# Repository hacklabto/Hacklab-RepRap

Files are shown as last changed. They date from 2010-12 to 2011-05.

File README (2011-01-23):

Prusa Mendel

Please read http://reprap.org/wiki/Hacklab_RepRap before attempting to build this.

When checking out from git, run the following to check out the MCAD dependencies:
	git submodule init
	git submodule update

Frame vertexes are based on Viks and Tonokips ones

Prusa Mendel part list:

To print:

6x frame-vertex
2x coupling
3x endstop-holder
1x x-carriage
1x x-end-idler
1x x-end-motor
2x z-motor-mount
4x belt-clamp
8x bar-clamp
2x rod-clamp
1x y-motor-bracket
2x pulley

3x pla-bushing

The Mendel build plate contains all the parts except the pla bushings

Vitamins required:

5/16 threaded rods - Measure these by assembling your parts to the build size you need and then figure out how long the rods need to be. (this sucks i know.. it's beta ;)
5/16 smooth rods - same
5/16 nuts - allot? I'd say 50-75?
some zip ties
teflon bushings
screws for your motors
4x nema 17 stepper motors
2x XXmm x 5mm T5 pitch timing belt

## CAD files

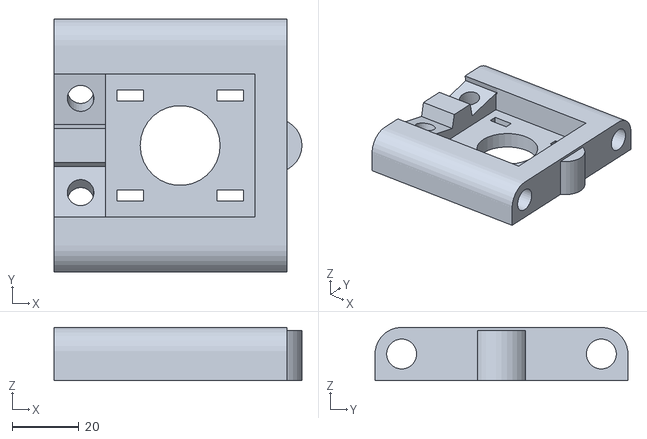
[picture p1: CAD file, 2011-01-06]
bin/z-motor-mount.stl
74.5 x 76.0 x 16.0

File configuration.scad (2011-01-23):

// PRUSA Mendel  
// Configuration file
// GNU GPL v2
// Josef Průša
// josefprusa@me.com
// prusadjs.cz
// http://www.reprap.org/wiki/Prusa_Mendel
// http://github.com/prusajr/PrusaMendel

//include <lib/mcad/motors.scad>
include <lib/mcad/nuts_and_bolts.scad>
include <constants.scad>

$fs= 0.3;

// Frame Design Settings
//=================

x_belt = true; //use belt or threaded rod for x-axis movement
               //threaded rod is currently broken. Do not use it.
               //Leave this true or be prepared to do lots of drilling!
               //Also, x-carriage doesn't support this option so you'll
               //have come up with a hack to make it work if you use this
               //option.

two_top_rods = true; //Use two top rods or one?
                      //No repraps have been built with one top, so use
                      //this design at your own risk!


//Spacing of the 2 smooth rods that the x carriage rides on
x_rod_spacing = 50;


// Build Volume Settings
//=================

//The x,y and z printable dimensions in that order
build_volume = [100,100,70];



// Threaded Rod Settings
//=================

//the diameter of the threaded rods
threaded_rod_diameter = 9;

//the radius of plastic needed around each threaded rod hole
//to hold it in place
threaded_rod_horizontal_clearance = 4;

//the plastic needed above and under each threaded rod hole
threaded_rod_vertical_clearance = 2;

nut_diameter=METRIC_NUT_AC_WIDTHS[8];//13.5;
nut_thickness = METRIC_NUT_THICKNESS[8]; //7.8;


tear_shape = false; //Use tear shaped holes for rods? not compatable with tight_grip = true

tight_grip = false; // Use tight holes where possible so that parts will self tap when 
                   // threaded rod is drilled in. Reduces need for nuts.
                   // tight_grip = false not compatable with two_top_rods = false



// Motor Settings
//=================

//NEMA_version //Variable not yet implemented.



//BS That Works
//=================

// unprintable height under the y carriage for motors + electronics.
// (rough estimate for vert angle calculations)
basement_height = 90;

// unprintable height from the bottom of the top frame vertex to 
// the point where the frame verticies meet.
// (rough estimate for vert angle calculations)
attic_height = 5;

//unprintable area due to the x ends/z-sliders
z_slider_unprintable_height = 70;

// extra length needed on the y axis to compensate for the 
// y-carriage's length. This is setup for the ABP carriage mount.
y_carriage_unprintable_length = 4;

//length from the middle of the bottom frame vertex to where the 
//frame triangle's threaded rods would meet if they were 
//extended to that point.
y_vert_triangle_offset = 2;

total_unprintable_area = [0,
	y_carriage_unprintable_length + y_vert_triangle_offset,
	basement_height+attic_height+z_slider_unprintable_height];


// Driven Dimensions [NO USER-CONFIGURABLE OPTIONS]
//=================

vert_angle = atan( 2*(build_volume[Z]+total_unprintable_area[Z])/(build_volume[Y]+total_unprintable_area[Y]));

echo("Frame Vertex Angle: ",vert_angle);

hor_hole_seperation = threaded_rod_diameter*2+threaded_rod_horizontal_clearance*2;



// Legacy
//=================

// DEPRECATED! M8 rod diameter. use threaded_rod_diameter
m8_diameter = threaded_rod_diameter;

// Used for $fn nut trick -> cylinder(h = 5, r=4.5, $fn=6, center=true);

//Diameter of the nuts used on the the threaded rod
//nut_diameter = 16.4;
//Clearance for accessible nuts such as on frame verticies
nut_clearance = 4;

//DEPRECATED! use nut_diameter
// M8 nut diameter diameter.
m8_nut_diameter = nut_diameter;

// M4 rod/screw diameter
m4_diameter = 5;

// M4 nut diameter diameter
// Used for $fn nut trick -> cylinder(h = 5, r=4.5, $fn=6, center=true);
m4_nut_diameter = METRIC_NUT_AC_WIDTHS[4]; //9;

// M3 rod/screw diameter
m3_diameter = 4.4;

// M3 nut diameter diameter
// Used for $fn nut trick -> cylinder(h = 5, r=4.5, $fn=6, center=true);
m3_nut_diameter = METRIC_NUT_AC_WIDTHS[3]; //7;

// Bushing holders diameter
bushing_diameter = 11;

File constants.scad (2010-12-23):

X = 0;
Y = 1;
Z = 2;

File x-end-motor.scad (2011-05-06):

// PRUSA Mendel  
// X-end with idler mount
// GNU GPL v2
// Rob Gilson, Christopher Olah
// http://reprap.org/wiki/Hacklab_RepRap
// https://github.com/hacklabto/Hacklab-RepRap

include <configuration.scad>
include <common.scad>
include <lib/mcad/nuts_and_bolts.scad>

thickness = 15;
length = 50;
width = 47.5;

bearing_inner_diameter = 7.5;

difference()
{
	union()
	{
		cube([width, length, thickness], center=true);
		//idler mount
		translate([width/2-2.5,width-4,-1])
			cube([5,47,45],center=true);
	}

	//holes for axis
	translate([0,-39,0]) x_axis_rods();
	for (x=[-1,1]) for(y=[-1,1]) translate([x*15,y*15,0]) ziptie_hole(thickness+1);
	translate([0,0,2]) z_nut_and_bushing_hole(thickness+1);
	#translate([width/2-11,width-1,-1]) rotate([0,-90,0]) motor();

}

module ziptie_hole(height)
{
	cube([5,10,height], center=true);
}

nut_and_bushing_seperation = 20;

module z_nut_and_bushing_hole(height=100)
{
	nut_radius = METRIC_NUT_AC_WIDTHS[8]/2+0.1;

	translate([0,-1.5*nut_radius-2]){
		cylinder(r=10, h=height, center=true);
		cylinder(r=4.3, h=1.5*height, center=true);
	}
	for (i=[1.4,1.5,1.6,1.75,1.9,2.0,2.1]) translate([0,i*nut_radius]){
		cylinder(r=4.3, h=1.5*height, center=true);
		linear_extrude(height = height, center = true)
			rotate(90) nutHole(size = 8, tolerance = +0.1, proj=1);
	}
	
}

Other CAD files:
y-end-motor-leadscrew.scad
bearing-pulley.scad
common.scad
coupling.scad
makerbot.scad
partlist.scad
prusalogo.scad
sanity_check.scad
vertex.scad
vertical-bar-clamp.scad
x-carriage-mendel.scad
x-carriage-mini.scad
x-carriage.scad
x-end-idler.scad
y-carriage-abp.scad
y-carriage-bushings.scad
y-carriage.scad
y-end-motor.scad
z-motor-mount.scad

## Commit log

2010-10-19 Initial add of Makefile and conditional rendering to makerbot.scad.
    [makerbot.scad]
2010-10-19 Reworked Makefile. Removed STL files created by scad or pulled from other sources (e.g. nophead pulley.stl).
    [bar-clamp.stl, belt-clamp.stl, coupling.stl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]
2010-11-13 UNTESTED: Lattice bottoms to avoid warping on x-carriage, x-end-motor. (Idea from clothbot.)
    [x-carriage.scad, x-end-motor.scad]
2010-11-13 Fixed stls, changed dicetion of x-carriage lattice.
    [x-carriage.scad, x-carriage.stl]
2010-11-13 Added x-end-motor.stl
    [x-end-motor.stl]
2010-11-13 Lattice replaced with a couple large grooves that should prevent warping similarily and be much easier to print in x-end-motor.
    [x-end-motor.scad, x-end-motor.stl]
2010-11-13 Grooves on x-carriage. Still not tested.
    [x-carriage.scad, x-carriage.stl]
2010-11-14 Revert "Lattice replaced with a couple large grooves that should prevent warping similarily and be much easier to print in x-end-motor."
    This reverts commit a599a914dad5de719b904652a9f80c7adc6e9a6b.
    [x-end-motor.scad, x-end-motor.stl]
2010-11-14 Some stuff from topmerge2 got into master. Can't seem to get rid of it. Commiting to change branches.
    [z-motor-mount.scad]
2010-11-16 Reworked top joint, reduces printed part count by 4, reduces knuts by self tapping threaded parts, and gets rid of one rod.
    [z-motor-mount.scad, z-motor-mount.stl]
2010-11-16 And this adds the one rod top version.
    [z-motor-mount-onerod.scad, z-motor-mount-onerod.stl]
2010-11-16 Minor cleanup, fixes.
    [z-motor-mount-onerod.scad, z-motor-mount-onerod.stl, z-motor-mount.scad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]
2010-11-16 Added z-motor-mount-onerod to Makefile.
2010-11-16 Merged z-motor-mount-onerod and z-motor-mount.
    [z-motor-mount-onerod.scad, z-motor-mount.scad]
2010-11-20 Added mcad with appropriate path changes.
    [configuration.scad]
2010-11-20 x-end-motor supports rod in place of belt, config and motor design for x-end-motor, z-motor-mount, motor design moved to configuration.scad.
    [configuration.scad, x-end-motor.scad, z-motor-mount.scad]
2010-11-20 Add x-bar support to x-end-motor.
    [x-end-idler.scad]
2010-11-21 the threaded x movement bar is broken. So I've made it *not* the default option. You can use it if you'd like, but you'll have to do lots of drilling.
    [configuration.scad]
2010-11-21 Y leadscrew motor mount, untested
    [configuration.scad, y-end-motor.scad]
2010-11-25 New 2 peice motor/leadscrew shaft coupler with zip ties and better shaft alignment
    [configuration.scad, coupling.scad]
2010-11-27 Began abstracting commmon components into common.scad, in particular, bar interfaces have been to ensure all parts will comply with standards.
    x_belt=false is still broken, though x-end-motor is done.
    [common.scad, configuration.scad, x-end-idler.scad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]
2010-11-28 x-end-idler is fixed. Yay!
    [configuration.scad, x-carriage.scad, x-end-idler.scad]
2010-11-30 Slimmed down x-end-idler.
    [x-end-idler.scad]
2010-12-18 y-carriage added for ABPs and frame vertex redesign for angle configuration and less wasted vertical space
    [configuration.scad, frame-vertex.scad, vertex-body-fixed-qcad.dxf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]
2010-12-18 x-end-idler redesign. Temporarily broken until x-end-motor catches up.
    [configuration.scad, x-end-idler.scad]
2010-12-18 Added a sanity check.
    [configuration.scad]
2010-12-18 automatically angled verticies driven by the build volume
    [configuration.scad, frame-vertex.scad]
2010-12-18 x-end-motor updated, though it may not be strong enough. Print test required.
    [common.scad, configuration.scad, x-end-motor.scad]
2010-12-18 Somehow anity check didn't get added when it was supposed to.
    [sanity_check.scad]
2010-12-19 added missing constants.scad file
    [constants.scad, frame-vertex.stl]
2010-12-21 z-motor-mount nows works with the new verteces, angle based.
    [common.scad, configuration.scad, z-motor-mount.scad]
2010-12-21 Adds partlist file. Compiles to give partlist. WIP
    [partlist.scad]
2010-12-23 Minor fix to z-motor-mount.
    [configuration.scad]
2010-12-24 avoid rebuilding everything - still not working for pulley.stl - why?
2010-12-29 changes from a while back
    [common.scad, configuration.scad, frame-vertex.scad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]
2010-12-29 new z motor mount binary
    [z-motor-mount.stl]
2011-01-06 Redesigned vertex, again!
    [configuration.scad, frame-vertex.scad]
2011-01-06 Somehow, this slipped by
    [vertex.scad]
2011-01-07 More vertex improvements.
    [configuration.scad, vertex.scad]
2011-01-09 added a new experimental (untested) x-carriage-mini for use with Ultimaker bowden extruders.
    [common.scad, configuration.scad, x-carriage-mini.scad]
2011-01-09 fixed vertex nut configuration, updated configuration parameters
    [configuration.scad, frame-vertex.stl, vertex.scad]
2011-01-09 Underside nut space for z-motor-mount.
    [z-motor-mount.scad]
2011-01-09 STLs should not be in git.
    [frame-vertex.stl]
2011-01-11 New z-motor-mount design puts the diagonal bars at the middle on the sides, reducing x length
    [common.scad, z-motor-mount.scad]
2011-01-14 cleared bottom and realized perpendicular rest for diagonal rod nuts
    [z-motor-mount.scad]
2011-01-19 y-motor-end changes i forgot to commit a long time ago
    [y-end-motor.scad, y-end-motor.stl]
2011-01-19 Experimenta y-carriage-bushings.scad for use with standard commercially available teflon bushings
    [y-carriage-bushings.scad]
2011-01-21 some vitamins added
    added x-carriage for normal bowden extruders
    Revert "added x-carriage for normal bowden extruders"
    This reverts commit 582c23b5c1cf0b5b179afa0ce0c2e0b694eedde6.
2011-01-21 consistent diameters
    [configuration.scad]
2011-01-21 as the x-idler-motor is about 65 mm high, the default should be able to print it
    [configuration.scad]
2011-01-21 parameterized wall thickness
    [x-end-idler.scad, x-end-motor.scad]
2011-01-23 Experimental z-motor-mounts
    [new-z-motor-mount.scad, new2-z-motor-mount.scad]
2011-01-23 Didn't mean to push to master.
    [new-z-motor-mount.scad, new2-z-motor-mount.scad]
2011-01-26 Fixed use syntax to match lib/mcad relative path.
    [prusalogo.scad]
2011-03-14 Rob's x-end-idler design.
    [x-end-idler.scad]
2011-03-17 Adds vertical-bar-clamp design.
    [vertical-bar-clamp.scad]
2011-03-17 Cleaned up the vertex code.
    [vertex.scad]
2011-05-06 Lots of work. Nearly at release candidate.
    [bearing-pulley.scad, vertex.scad, vertical-bar-clamp.scad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]
2011-05-11 Misc improvements.
    [x-carriage-mendel.scad, z-motor-mount.scad]
2011-05-11 Cut z-motor-mount for easier assembly.
    [z-motor-mount.scad]
